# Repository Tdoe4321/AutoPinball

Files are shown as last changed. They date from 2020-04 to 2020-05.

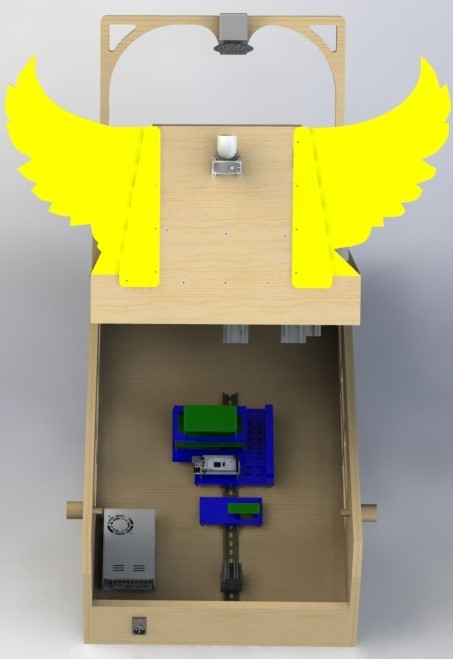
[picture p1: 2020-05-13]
CAD_Models/Play Field/Renderings/Final Renderings/Electronics 1.JPG

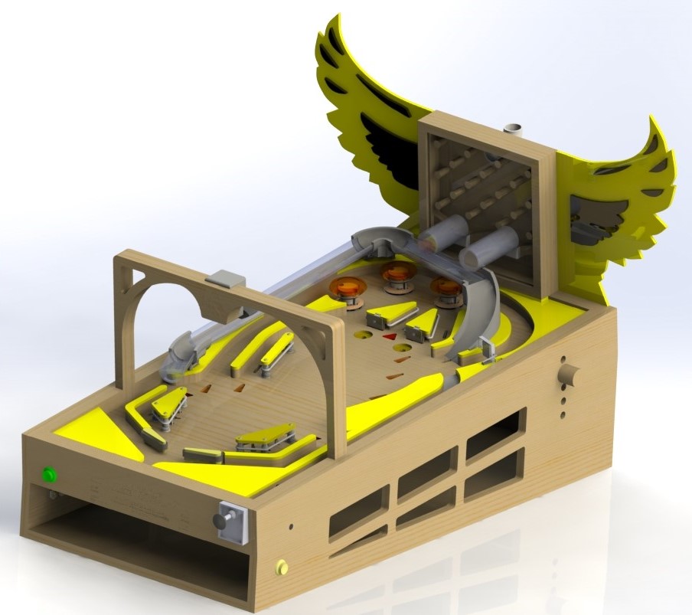
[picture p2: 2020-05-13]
CAD_Models/Play Field/Renderings/Isometric 4.JPG

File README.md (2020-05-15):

# AutoPinball
A custom pinball machine that plays itself!

[Checkout the full Instructables post!](https://www.instructables.com/id/Arduino-Pinball-Machine-That-Plays-Itself)

Check out the video here:  
AutoPinball Video (https://www.youtube.com/watch?v=dy7oVSNtaRk "AutoPinball")

Straight up demonstration of the autonomy here:  
AutoPinball Demonstration (https://www.youtube.com/watch?v=hW7z0yfWGfI "AutoPinball")

### Dependencies
This repo has the following dependencies that must be installed.
 * [ROS](http://wiki.ros.org/melodic/Installation/Ubuntu)
 * [rosserial_arduino](http://wiki.ros.org/rosserial_arduino/Tutorials/Arduino%20IDE%20Setup)
 * [OpenCV C++](https://opencv.org/)
 * [Tkinter](https://docs.python.org/3/library/tkinter.html)
 * [APScheduler](https://apscheduler.readthedocs.io/en/stable/)
 
To install ROS and rosserial_arduino, follow the links above and install as normal, for everything else, do the following:

```bash
sudo apt install libopencv-dev python3-opencv # OpenCV
sudo apt install python-tk # Tkinter
pip install APScheduler  # APScheduler
```
 
### Build
To build the system do the following:
```bash
cd /path/to/AutoPinball
mkdir build
cd build
cmake ..
make
source devel/setup.bash
```

After you build it, you can put the `source` command into your `~/.bashrc` to have it automatically source the directory whenever you start up a new bash shell. Just make sure that you give the full path, ex:  
`/home/<my-username>/AutoPinball/build/devel/setup.bash`

### RUN IT!
There's a few different launch files that you can use depending on what you want to do.
If you want to run the whole thing, run this one from the `launch` directory:  
```bash
roslaunch automatic_pinball_c.launch
```

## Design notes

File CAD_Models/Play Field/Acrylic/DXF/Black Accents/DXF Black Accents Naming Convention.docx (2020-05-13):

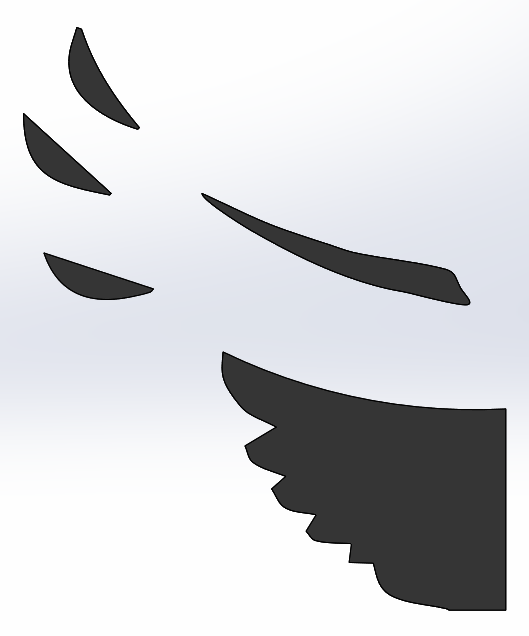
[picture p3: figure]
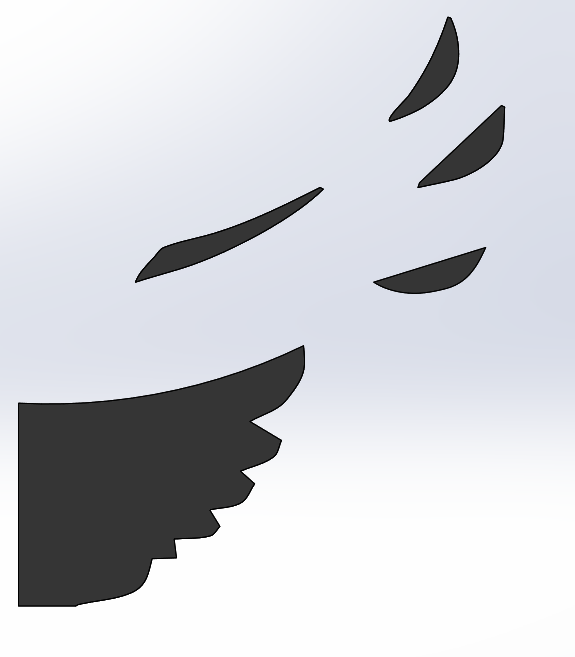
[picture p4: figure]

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
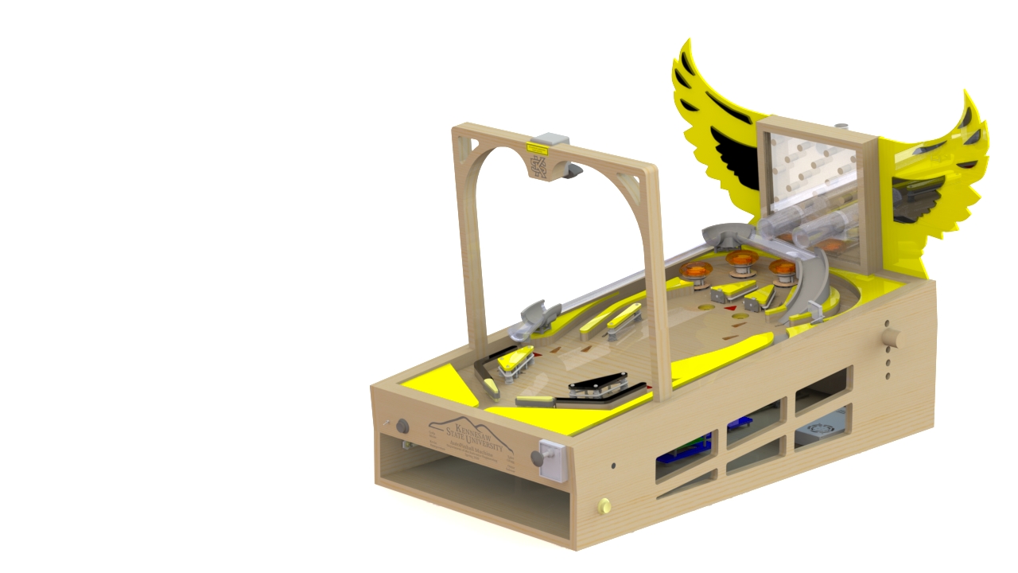
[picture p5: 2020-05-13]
CAD_Models/Play Field/Renderings/Final Renderings/16-9 Dimetric Thumbnail.JPG

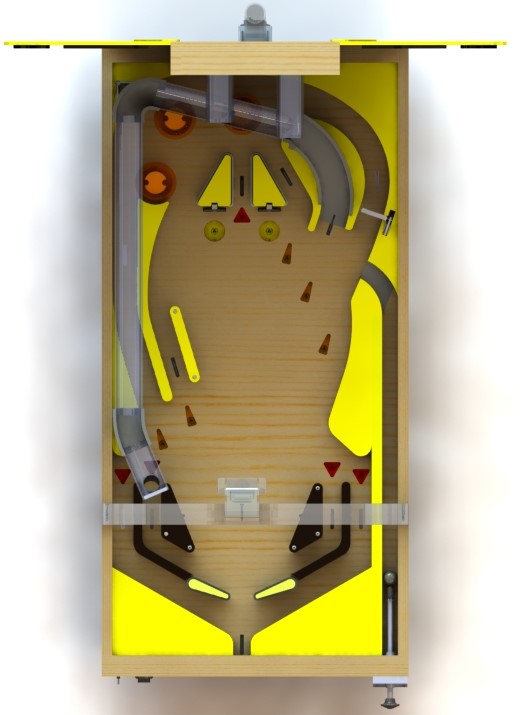
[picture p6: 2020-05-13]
CAD_Models/Play Field/Renderings/Final Renderings/Top 3.JPG

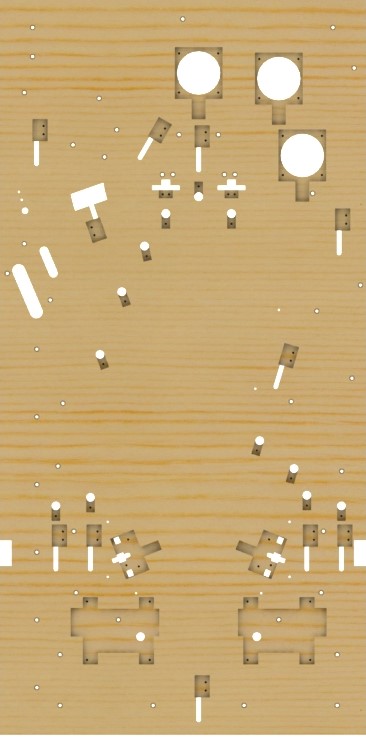
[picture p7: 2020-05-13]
CAD_Models/Play Field/Renderings/Final Renderings/Playfield Bottom 1.JPG

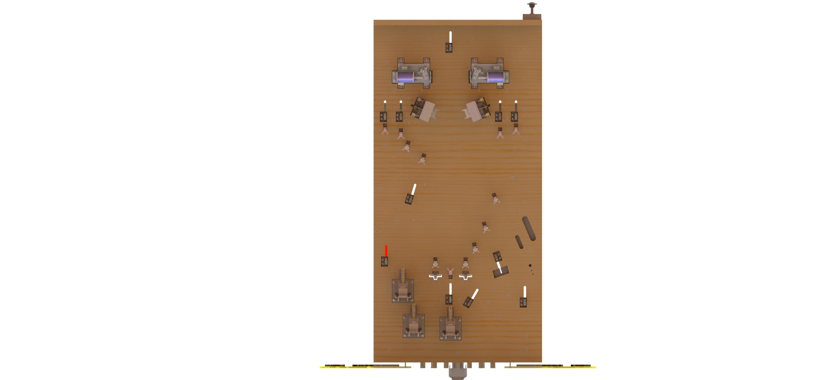
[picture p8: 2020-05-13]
CAD_Models/Play Field/Renderings/Bottom - 2.JPG

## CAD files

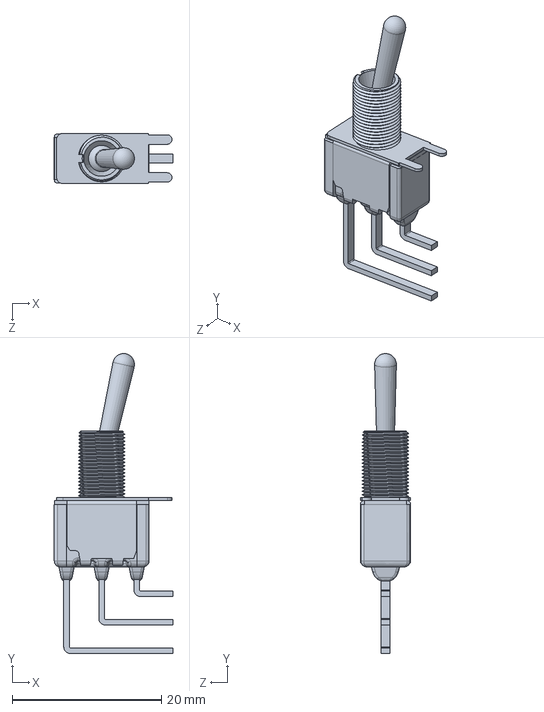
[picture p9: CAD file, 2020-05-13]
CAD_Models/Components/Electrical/7103SYAV2BE.SLDASM
15.9 x 40.2 x 6.76 mm

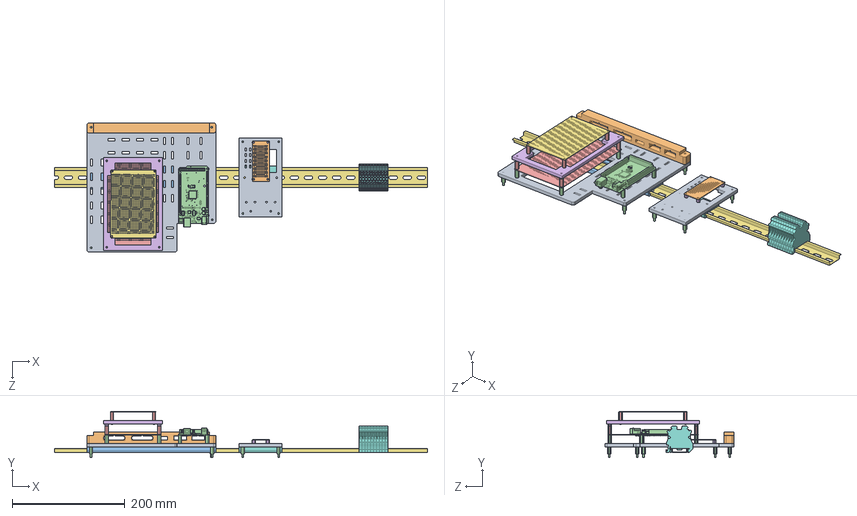
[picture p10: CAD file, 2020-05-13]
CAD_Models/Components/Electrical/Final_Pinball_Control_board/Main_Assembly/Final_Assembly.SLDASM
660.4 x 81.7 x 228.6 mm
Main board
Connector_Holder
Main board din_rail
arduinoMega
Flipper board
LED_mount
LED_control_board
Output board din rail
Output board
Output_Board
Spacer_Nut x 12
Spacer_.592 x 16
Spacer_.778 x 8
Spacer_..237 x 8
1.00m DIN Rail
UT_2.5_BK-select.stp x 10

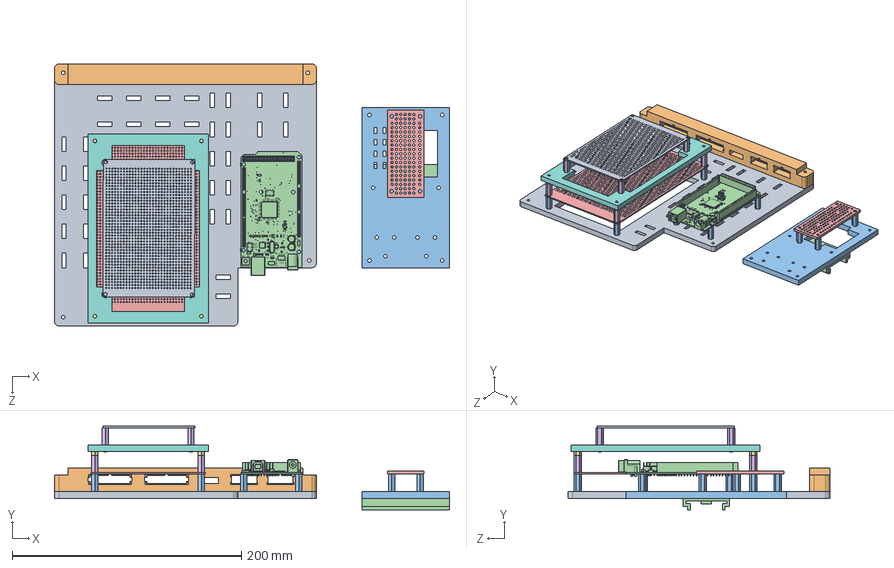
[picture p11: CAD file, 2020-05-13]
CAD_Models/Components/Electrical/Final_Pinball_Control_board_2/Main_Assembly/Final_Assembly.SLDASM
344.8 x 73.2 x 228.6 mm
Main board
Spacer_Nut x 18
Spacer_.592 x 12
arduinoMega
Flipper board
Spacer_.778 x 8
Spacer_..237 x 4
LED_mount
LED_control_board
Connector_Holder
Output board
Output

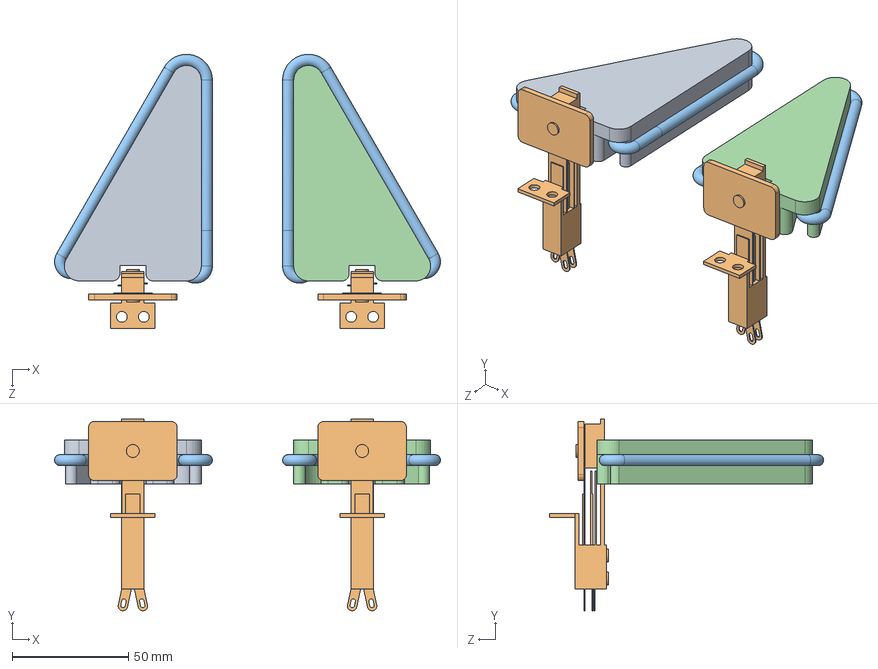
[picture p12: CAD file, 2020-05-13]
CAD_Models/Play Field/Play Items/Triangle Centerpiece Assembly R0.2.SLDASM
165.9 x 82.4 x 117.9 mm
Center Triangle Boundary R0.3
Stand-Up Target x 2
2.50 Elastic Band - Triangle x 2
Center Triangle Boundary R0.3 - Right

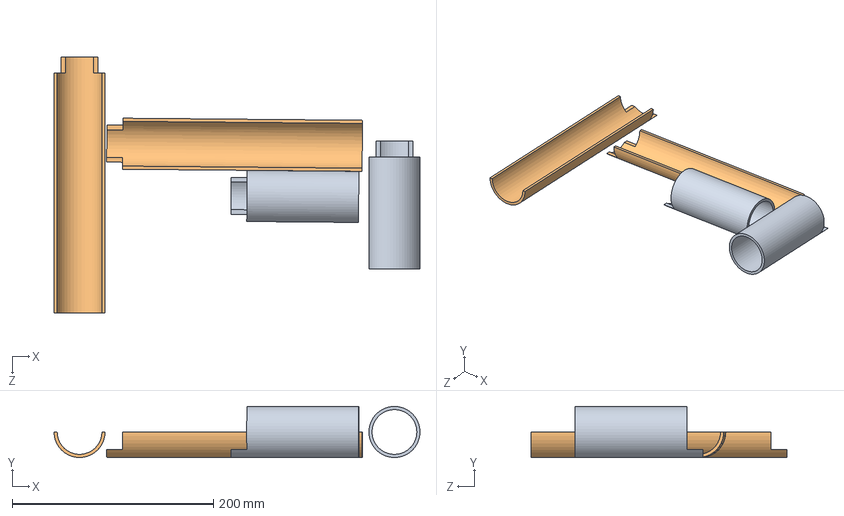
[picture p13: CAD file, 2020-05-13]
CAD_Models/Play Field/Reference & Testing/Tube Fitting Testing Assembly.SLDASM
363.8 x 50.8 x 254.0 mm
Pachinko Tube Acrylic x 2
Pachinko Tube Acrylic Halved x 2

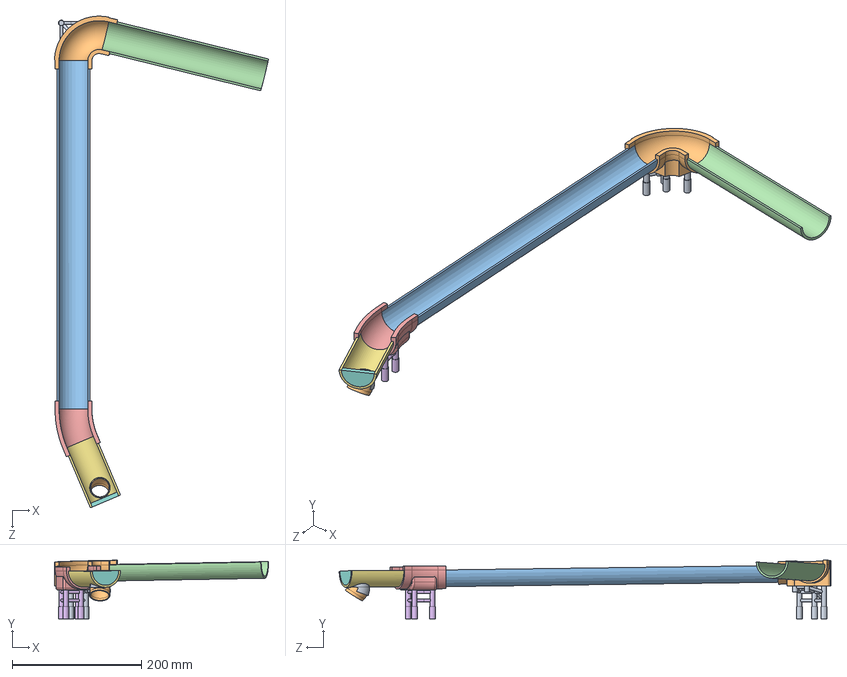
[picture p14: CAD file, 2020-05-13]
CAD_Models/Play Field/Second Level/Second Level Tube Assembly.SLDASM
331.5 x 90.9 x 761.6 mm
Joint 1 Mount
2.00 Acrylic Tube Adapter - 76.2deg
Level 2 Halved Tube - 2
Level 2 Halved Tube - 1
2.00 Acrylic Tube Adapter - 23.0deg
Joint 2 Mount R0.2
Level 2 Halved Tube - 3
1.75 x 0.125 Acrylic Tube End Cap - Halved
Second Level Drop Guide
Second Level Drop Guide R0.2

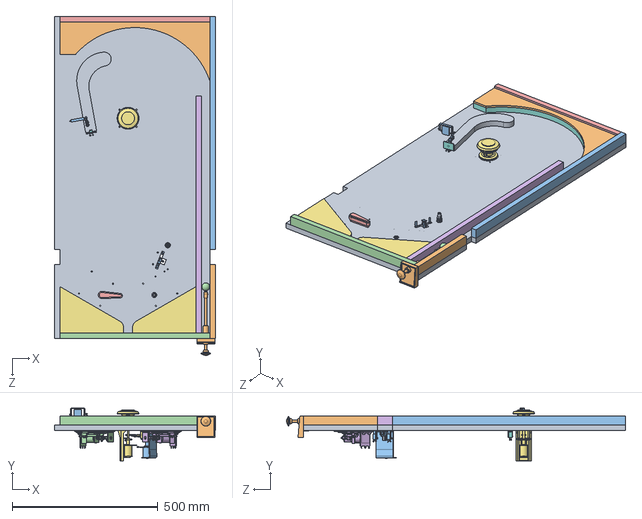
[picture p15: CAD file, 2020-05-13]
CAD_Models/Play Field/Subsystem Demo/AutoPinball Subsystem Demo Playfield.SLDASM
552.5 x 180.6 x 1163.4 mm

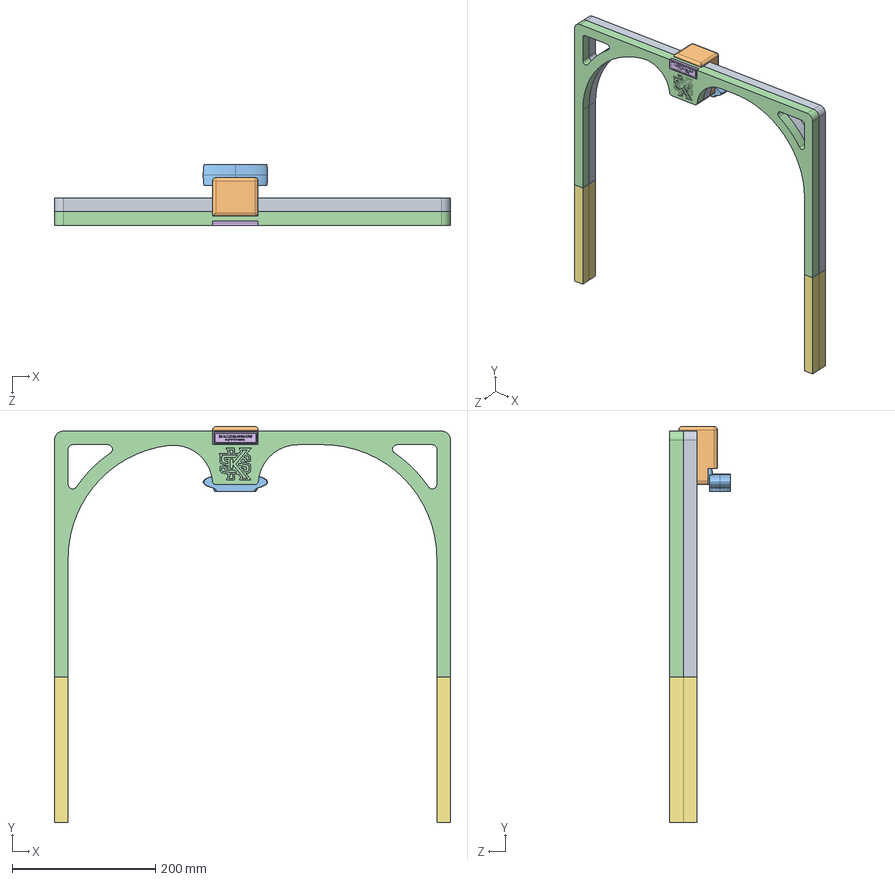
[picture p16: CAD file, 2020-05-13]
CAD_Models/Play Field/Camera Mount/Layered Concepts/Camera Mount Layered Concept 1.SLDASM
552.5 x 552.5 x 84.6 mm
Camera Mount Layered Concept 1
Camera Mount
Web Camera
Camera Mount Layered Concept 1 - Mirrored R0.2
#8 x 1.250 Flat Phillips Head for Wood AISI 304 x 3
Camera Mount Engraving Acrylic x 2
Camera Mount Leg Extensions x 4

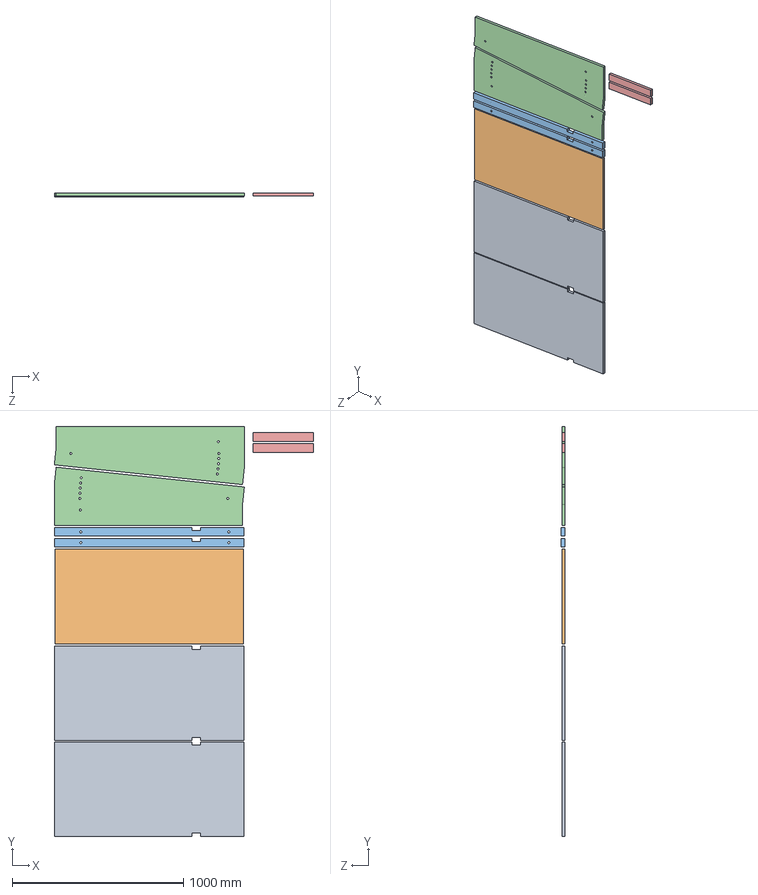
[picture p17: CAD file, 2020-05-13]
CAD_Models/Play Field/Reference & Testing/Plywood Order.SLDASM
1513.9 x 2392.7 x 25.4 mm
Base Layer R0.2 x 2
Base Stand
Playfield Support Strut x 2
Side Stand R0.2 x 2
Camera Mount Support Strut x 2

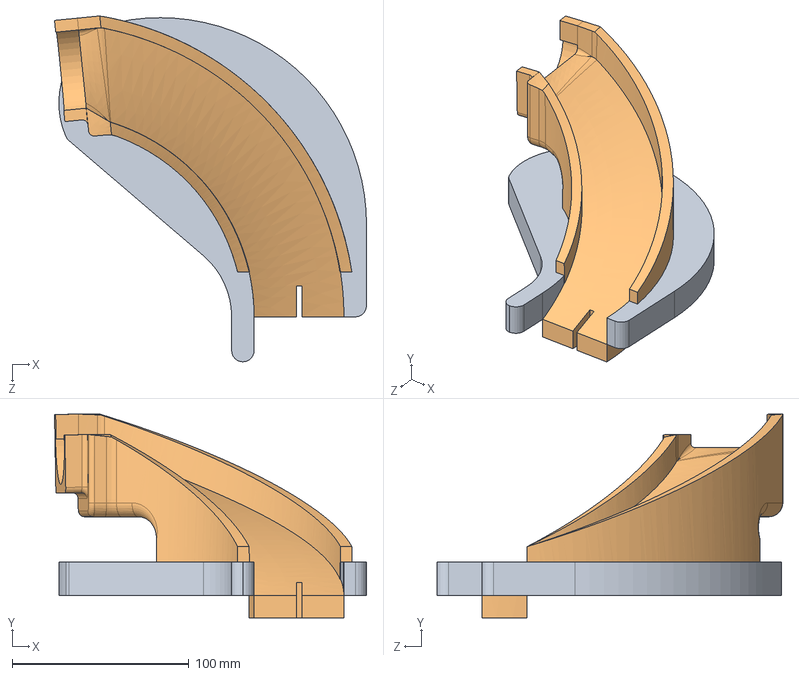
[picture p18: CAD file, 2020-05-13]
CAD_Models/Play Field/Second Level/Playfield Ramp Assembly.SLDASM
176.4 x 115.2 x 195.4 mm
Ramp Base Mount
Playfield Ramp
#8-32 x 0.321 Brass Flanged Heat Insert x 4

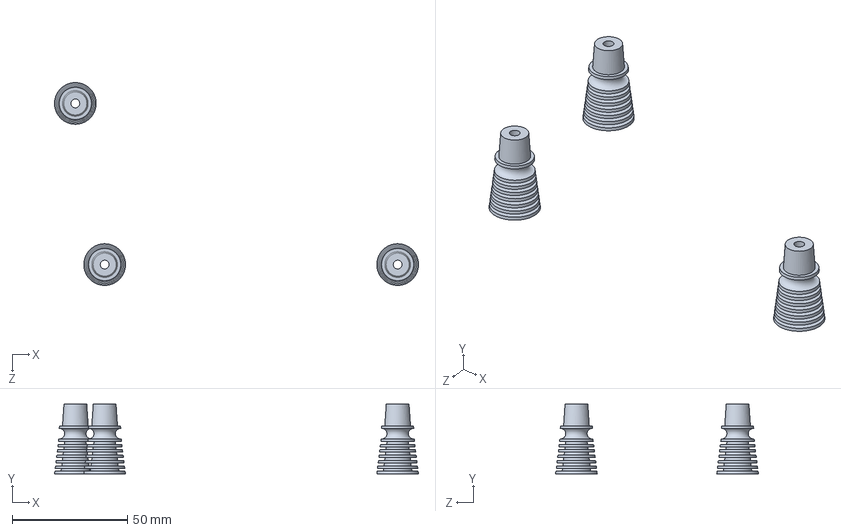
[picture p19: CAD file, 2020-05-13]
CAD_Models/Components/3.00 Elastic Band Triangle.SLDASM
157.8 x 30.2 x 87.9 mm
Star Post - Clear x 3

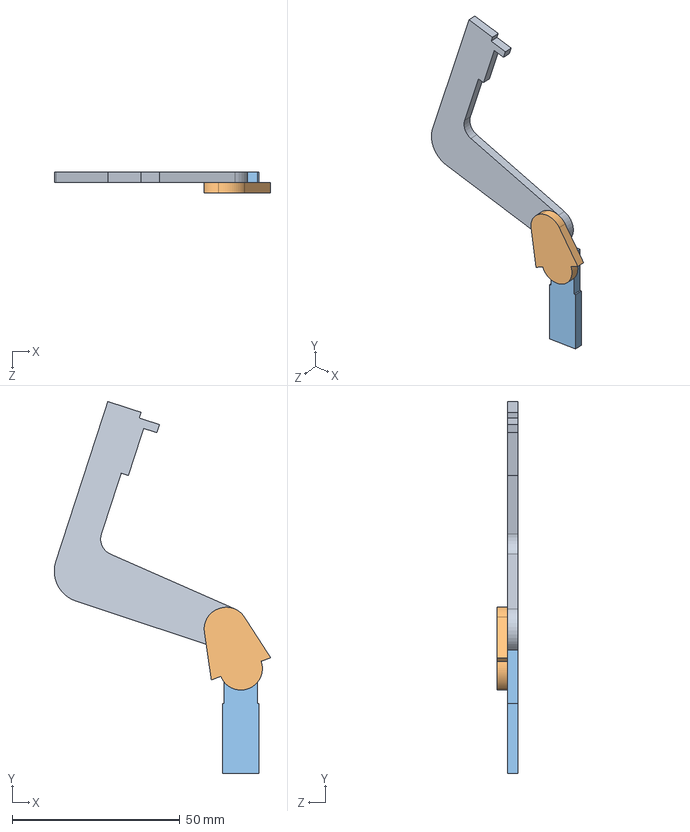
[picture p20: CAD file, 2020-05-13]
CAD_Models/Components/Cams/Slingshot Test Cam Assembly.SLDASM
64.4 x 110.7 x 6.35 mm
Slingshot Test Cam
Slingshot Test Cam Adapter
Slingshot Test Cam Solenoid Rod

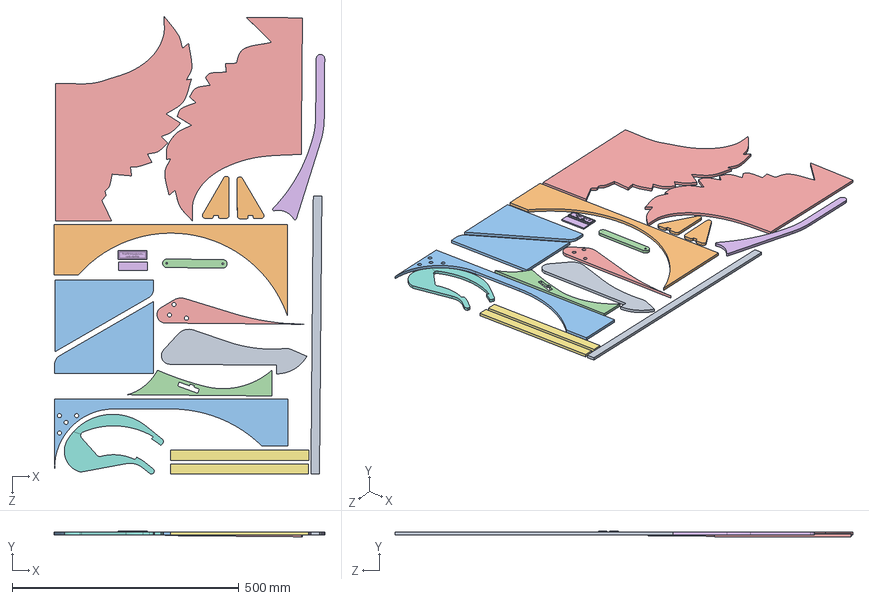
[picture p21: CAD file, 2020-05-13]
CAD_Models/Play Field/Acrylic/Yellow Acrylic Layout.SLDASM
596.0 x 12.4 x 1008.9 mm
Shooter Trim Acrylic
Center Triangle Boundary R0.3 Acrylic x 2
Front Apron Acrylic x 2
Launch Lane Exit Guard - Right Acrylic
Left Outlane Guard Acrylic
Left Y-Lane Trim Acrylic
Pachinko Machine Shim Acrylic x 2
Ramp Base Mount Acrylic
Right Outlane Guard Acrylic
Top Apron Acrylic
Top Apron Acrylic R0.2
Y-Lane Elastic Acrylic
KSU Owl Wings - Left x 2
Camera Mount Engraving Acrylic x 2

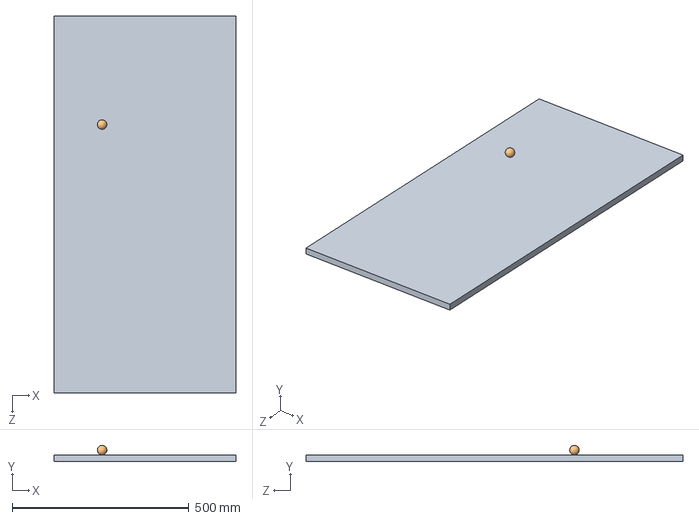
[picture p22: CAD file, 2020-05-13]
CAD_Models/Play Field/AutoPinball Playfield R0.1.SLDASM
514.3 x 46.0 x 1066.8 mm
Base Layer 6deg Gradient
Standard Pinball

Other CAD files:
CAD_Models/Play Field/CNC/Extra/THRU MILL AND 0.25 DP MILL AND 0.125 X 0.4375 DP BIT AND 0.125 THRU ALL BIT - EXTRA.SLDASM
CAD_Models/Play Field/CNC/THRU MILL 2D LAYOUT - EXTRA/THRU MILL 2D LAYOUT - EXTRA.SLDASM
CAD_Models/Play Field/CNC/THRU MILL AND 0.125 X 0.4375 DP BIT - EXTRA/THRU MILL AND 0.125 X 0.4375 DP BIT - EXTRA.SLDASM
CAD_Models/Play Field/CNC/Stand/THRU MILL - STAND.SLDASM
CAD_Models/Components/0.25 x 20 x 1.25 Five Arm Knob.SLDPRT
CAD_Models/Components/2.0 Elastic Band - Y-Lane.SLDPRT
CAD_Models/Components/2.00 Elastic Band - Slingshot.SLDPRT
CAD_Models/Components/2.00 Elastic Band Triangle R0.2.SLDASM
CAD_Models/Components/2.00 Elastic Band Triangle.SLDASM
CAD_Models/Components/2.25 Elastic Band - Y-Lane.SLDPRT
CAD_Models/Components/2.25 Elastic Band Triangle R0.2.SLDASM
CAD_Models/Components/2.25 Elastic Band Triangle.SLDASM
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

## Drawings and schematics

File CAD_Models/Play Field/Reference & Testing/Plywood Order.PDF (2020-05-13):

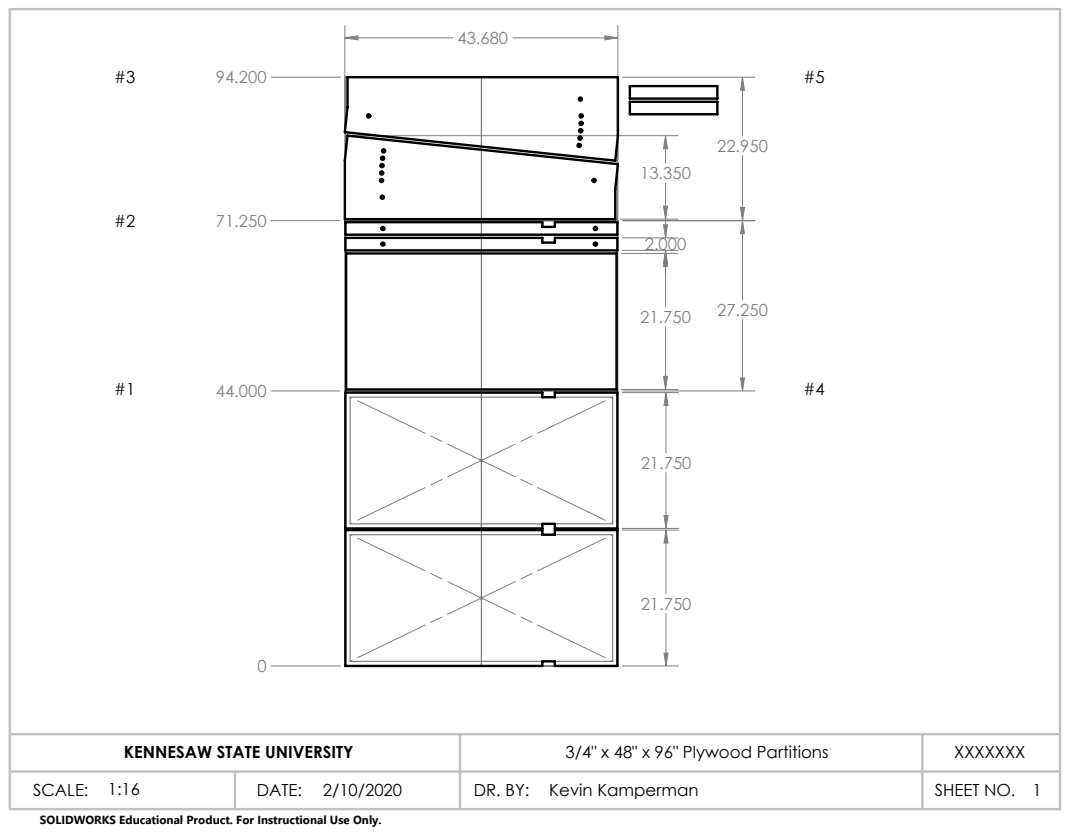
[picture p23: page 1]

KENNESAW STATE UNIVERSITY | 3/4" x 48" x 96" Plywood Partitions | XXXXXXX

1:16 SCALE: | DATE: 2/10/2020 | DR. BY: Kevin Kamperman | SHEET NO. 1

SOLIDWORKS Educational Product. For Instructional Use Only.

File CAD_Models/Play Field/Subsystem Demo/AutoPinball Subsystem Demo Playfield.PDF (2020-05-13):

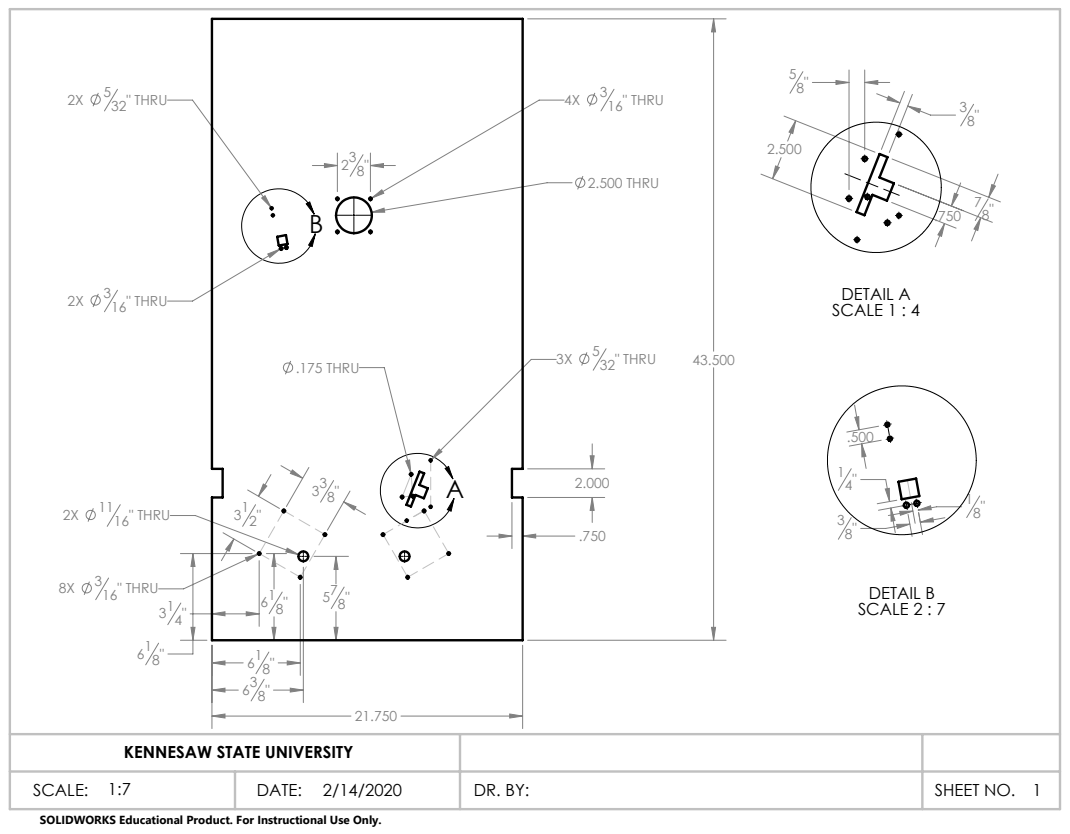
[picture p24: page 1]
2.500 THRU; " THRU 5; 32" THRU; 2X 3 16" THRU; .175 THRU; 8X 3 16" THRU; 2X 11 16" THRU; DETAIL A SCALE 1 : 4; DETAIL B SCALE 2 : 7

KENNESAW STATE UNIVERSITY

SCALE: 1:7 | DATE: 2/14/2020 | DR. BY: | SHEET NO. 1

SOLIDWORKS Educational Product. For Instructional Use Only.

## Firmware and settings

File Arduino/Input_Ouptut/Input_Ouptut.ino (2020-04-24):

/*
 * Author: Tyler Gragg
 * Date First Created: 01/18/2020
 * Project: AutoPinball
 */

#include <ros.h>
#include <std_msgs/Int32.h>
#include <std_msgs/UInt16.h>
#include <std_msgs/Bool.h>
#include <Servo.h>

// Flipper Outputs
#define LeftFlipper 20
#define RightFlipper 21


// Switch Inputs - Playfield
// TOP
#define TopSwitch0 8  // Rollover
#define TopSwitch1 49 // Bumper
#define TopSwitch2 50 // Bumper
#define TopSwitch3 51 // Bumper
#define TopSwitch4 5  // Rollover
#define TopSwitch5 15 // Spinner

// MID
#define MidSwitch0 9  // Rollover
#define MidSwitch1 13 // Standup
#define MidSwitch2 7  // Rollover
#define MidSwitch3 14 // Standup
#define MidSwitch4 6  // Rollover
#define MidSwitch5 4  // Rollover

//BOT
#define BotSwitch0 10 // Rollover
#define BotSwitch1 11 // Rollover
#define BotSwitch2 53 // Slingshot
#define BotSwitch3 52 // Slingshot
#define BotSwitch4 3  // Rollover
#define BotSwitch5 2  // Rollover
#define BotSwitch6 18 // Flipper
#define BotSwitch7 19 // Flipper
#define BotSwitch8 12 // Rollover

// Light Outputs
// TOP
#define TopLight0 36
#define TopLight1 35
#define TopLight2 34

// MID
#define MidLight0 31
#define MidLight1 32
#define MidLight2 27
#define MidLight3 28
#define MidLight4 29
#define MidLight5 26
#define MidLight6 25
#define MidLight7 24

// BOT
#define BotLight0 33
#define BotLight1 30
#define BotLight2 23
#define BotLight3 22

// Coils
#define Coil0 44
#define Coil1 45
#define Coil2 46
#define Coil3 47
#define Coil4 48

// Start button & Autonomy Switch
#define StartButton 42
#define AutonomySwitch 43

// Servo for the multiball
#define ServoPin A0
Servo multiball; 

// Last states
// TOP
uint8_t TopSwitch0Last = 0;
uint8_t TopSwitch1Last = 0;
uint8_t TopSwitch2Last = 0;
uint8_t TopSwitch3Last = 0;
uint8_t TopSwitch4Last = 0;
uint8_t TopSwitch5Last = 0;

// MID
uint8_t MidSwitch0Last = 0;
uint8_t MidSwitch1Last = 0;
uint8_t MidSwitch2Last = 0;
uint8_t MidSwitch3Last = 0;
uint8_t MidSwitch4Last = 0;
uint8_t MidSwitch5Last = 0;

// BOT
uint8_t BotSwitch0Last = 0;
uint8_t BotSwitch1Last = 0;
uint8_t BotSwitch2Last = 0;
uint8_t BotSwitch3Last = 0;
uint8_t BotSwitch4Last = 0;
uint8_t BotSwitch5Last = 0;
uint8_t BotSwitch6Last = 0;
uint8_t BotSwitch7Last = 0;
uint8_t BotSwitch8Last = 0;

uint8_t StartButtonLast = 0;
uint8_t AutonomySwitchLast = 0;

// ROS Node Handle
ros::NodeHandle nh;

// ROS Published messages
std_msgs::Bool empty_msg;

// TOP
ros::Publisher switch_top_0_pub("switch_top_0_triggered", &empty_msg);
ros::Publisher switch_top_1_pub("switch_top_1_triggered", &empty_msg);
ros::Publisher switch_top_2_pub("switch_top_2_triggered", &empty_msg);
ros::Publisher switch_top_3_pub("switch_top_3_triggered", &empty_msg);
ros::Publisher switch_top_4_pub("switch_top_4_triggered", &empty_msg);
ros::Publisher switch_top_5_pub("switch_top_5_triggered", &empty_msg);

// MID
ros::Publisher switch_mid_0_pub("switch_mid_0_triggered", &empty_msg);
ros::Publisher switch_mid_1_pub("switch_mid_1_triggered", &empty_msg);
ros::Publisher switch_mid_2_pub("switch_mid_2_triggered", &empty_msg);
ros::Publisher switch_mid_3_pub("switch_mid_3_triggered", &empty_msg);
ros::Publisher switch_mid_4_pub("switch_mid_4_triggered", &empty_msg);
ros::Publisher switch_mid_5_pub("switch_mid_5_triggered", &empty_msg);

// BOT
ros::Publisher switch_bot_0_pub("switch_bot_0_triggered", &empty_msg);
ros::Publisher switch_bot_1_pub("switch_bot_1_triggered", &empty_msg);
ros::Publisher switch_bot_2_pub("switch_bot_2_triggered", &empty_msg);
ros::Publisher switch_bot_3_pub("switch_bot_3_triggered", &empty_msg);
ros::Publisher switch_bot_4_pub("switch_bot_4_triggered", &empty_msg);
ros::Publisher switch_bot_5_pub("switch_bot_5_triggered", &empty_msg);
ros::Publisher switch_bot_6_pub("switch_bot_6_triggered", &empty_msg);
ros::Publisher switch_bot_7_pub("switch_bot_7_triggered", &empty_msg);
ros::Publisher switch_bot_8_pub("switch_bot_8_triggered", &empty_msg);

ros::Publisher start_button_pub("switch_start_button_triggered", &empty_msg);
ros::Publisher autonomy_switch_pub("switch_autonomy_switch_triggered", &empty_msg);

void flip_callback(const std_msgs::Int32& flipper){
  // 1 = left_flipper ON, 2 = right_flipper ON, -1 = left_flipper OFF, -2 = right_flipper OFF
  if (flipper.data == 1){
    digitalWrite(LeftFlipper, HIGH);
  }
  else if(flipper.data == 2){
    digitalWrite(RightFlipper, HIGH); 
  }
  else if(flipper.data == -1){
    digitalWrite(LeftFlipper, LOW);
  }
  else if(flipper.data == -2){
    digitalWrite(RightFlipper, LOW);
  }
}

// Turn on whatever int comes in
void pin_on_callback(const std_msgs::Int32& pin){
  digitalWrite(pin.data, HIGH);
}

// Turn off whatever int comes in
void pin_off_callback(const std_msgs::Int32& pin){
  digitalWrite(pin.data, LOW);
}

// Write the servo to whatever comes in
void servo_value_callback(const std_msgs::UInt16& value){
  multiball.writeMicroseconds(value.data); 
}


// ROS Subscibed messages
ros::Subscriber<std_msgs::Int32> flip_sub("flip_flipper", &flip_callback);
ros::Subscriber<std_msgs::Int32> pin_on_sub("pin_on", &pin_on_callback);
ros::Subscriber<std_msgs::Int32> pin_off_sub("pin_off", &pin_off_callback);
ros::Subscriber<std_msgs::UInt16> multiball_servo_sub("servo_value", &servo_value_callback);

// Check all switches, then publish if they are triggered
void checkSwitches(){
  //TOP
  uint8_t curTopSwitch0 = digitalRead(TopSwitch0);
  uint8_t curTopSwitch1 = digitalRead(TopSwitch1);
  uint8_t curTopSwitch2 = digitalRead(TopSwitch2);
  uint8_t curTopSwitch3 = digitalRead(TopSwitch3);
  uint8_t curTopSwitch4 = digitalRead(TopSwitch4);
  uint8_t curTopSwitch5 = digitalRead(TopSwitch5);

  //MID
  uint8_t curMidSwitch0 = digitalRead(MidSwitch0);
  uint8_t curMidSwitch1 = digitalRead(MidSwitch1);
  uint8_t curMidSwitch2 = digitalRead(MidSwitch2);
  uint8_t curMidSwitch3 = digitalRead(MidSwitch3);
  uint8_t curMidSwitch4 = digitalRead(MidSwitch4);
  uint8_t curMidSwitch5 = digitalRead(MidSwitch5);
  
  //BOT
  uint8_t curBotSwitch0 = digitalRead(BotSwitch0);
  uint8_t curBotSwitch1 = digitalRead(BotSwitch1);
  uint8_t curBotSwitch2 = digitalRead(BotSwitch2);
  uint8_t curBotSwitch3 = digitalRead(BotSwitch3);
  uint8_t curBotSwitch4 = digitalRead(BotSwitch4);
  uint8_t curBotSwitch5 = digitalRead(BotSwitch5);
  uint8_t curBotSwitch6 = digitalRead(BotSwitch6);
  uint8_t curBotSwitch7 = digitalRead(BotSwitch7);
  uint8_t curBotSwitch8 = digitalRead(BotSwitch8);

  uint8_t curStartButton = digitalRead(StartButton);
  uint8_t curAutonomySwitch = digitalRead(AutonomySwitch);
  
  // -----------  TOP  -----------
  if (!curTopSwitch0 && curTopSwitch0 != TopSwitch0Last){
    switch_top_0_pub.publish(&empty_msg);
    nh.spinOnce();
  }
  if (!curTopSwitch1 && curTopSwitch1 != TopSwitch1Last){
    switch_top_1_pub.publish(&empty_msg);
    nh.spinOnce();
  }
  if (!curTopSwitch2 && curTopSwitch2 != TopSwitch2Last){
    switch_top_2_pub.publish(&empty_msg);
    nh.spinOnce();
  }
  if (!curTopSwitch3 && curTopSwitch3 != TopSwitch3Last){
    switch_top_3_pub.publish(&empty_msg);
    nh.spinOnce();
  }
  if (!curTopSwitch4 && curTopSwitch4 != TopSwitch4Last){
    switch_top_4_pub.publish(&empty_msg);
    nh.spinOnce();
  }
  if (!curTopSwitch5 && curTopSwitch5 != TopSwitch5Last){
    switch_top_5_pub.publish(&empty_msg);
    nh.spinOnce();
  }

  // -----------  MID  -----------
  if (!curMidSwitch0 && curMidSwitch0 != MidSwitch0Last){
    switch_mid_0_pub.publish(&empty_msg);
    nh.spinOnce();
  }
  if (!curMidSwitch1 && curMidSwitch1 != MidSwitch1Last){
    switch_mid_1_pub.publish(&empty_msg);
    nh.spinOnce();
  }
  if (!curMidSwitch2 && curMidSwitch2 != MidSwitch2Last){
    switch_mid_2_pub.publish(&empty_msg);
    nh.spinOnce();
  }
  if (!curMidSwitch3 && curMidSwitch3 != MidSwitch3Last){
    switch_mid_3_pub.publish(&empty_msg);
    nh.spinOnce();
  }
  if (!curMidSwitch4 && curMidSwitch4 != MidSwitch4Last){
    switch_mid_4_pub.publish(&empty_msg);
    nh.spinOnce();
  }
  if (!curMidSwitch5 && curMidSwitch5 != MidSwitch5Last){
    switch_mid_5_pub.publish(&empty_msg);
    nh.spinOnce();
  }

  // -----------  BOT  -----------
  if (!curBotSwitch0 && curBotSwitch0 != BotSwitch0Last){
    switch_bot_0_pub.publish(&empty_msg);
    nh.spinOnce();
  }
  if (!curBotSwitch1 && curBotSwitch1 != BotSwitch1Last){
    switch_bot_1_pub.publish(&empty_msg);
    nh.spinOnce();
  }
  if (!curBotSwitch2 && curBotSwitch2 != BotSwitch2Last){
    switch_bot_2_pub.publish(&empty_msg);
    nh.spinOnce();
  }
  if (!curBotSwitch3 && curBotSwitch3 != BotSwitch3Last){
    switch_bot_3_pub.publish(&empty_msg);
    nh.spinOnce();
  }
  if (!curBotSwitch4 && curBotSwitch4 != BotSwitch4Last){
    switch_bot_4_pub.publish(&empty_msg);
    nh.spinOnce();
  }
  if (!curBotSwitch5 && curBotSwitch5 != BotSwitch5Last){
    switch_bot_5_pub.publish(&empty_msg);
    nh.spinOnce();
  }
  if (curBotSwitch6 && curBotSwitch6 != BotSwitch6Last){ // FLIPPER - different logic
    switch_bot_6_pub.publish(&empty_msg);
    nh.spinOnce();
  }
  if (curBotSwitch7 && curBotSwitch7 != BotSwitch7Last){ // FLIPPER - different logic
    switch_bot_7_pub.publish(&empty_msg);
    nh.spinOnce();
  }
  if (!curBotSwitch8 && curBotSwitch8 != BotSwitch8Last){
    switch_bot_8_pub.publish(&empty_msg);
    nh.spinOnce();
  }

  // -----------  OTHER  -----------
  if (!curStartButton && curStartButton != StartButtonLast){
    start_button_pub.publish(&empty_msg);
    nh.spinOnce();
  }
  if (curAutonomySwitch!= AutonomySwitchLast){
    empty_msg.data = !curAutonomySwitch;
    autonomy_switch_pub.publish(&empty_msg);
    nh.spinOnce();
  }

  //TOP
  TopSwitch0Last = curTopSwitch0;
  TopSwitch1Last = curTopSwitch1;
  TopSwitch2Last = curTopSwitch2;
  TopSwitch3Last = curTopSwitch3;
  TopSwitch4Last = curTopSwitch4;
  TopSwitch5Last = curTopSwitch5;
    
  //MID
  MidSwitch0Last = curMidSwitch0;
  MidSwitch1Last = curMidSwitch1;
  MidSwitch2Last = curMidSwitch2;
  MidSwitch3Last = curMidSwitch3;
  MidSwitch4Last = curMidSwitch4;
  MidSwitch5Last = curMidSwitch5;
  
  //BOT
  BotSwitch0Last = curBotSwitch0;
  BotSwitch1Last = curBotSwitch1;
  BotSwitch2Last = curBotSwitch2;
  BotSwitch3Last = curBotSwitch3;
  BotSwitch4Last = curBotSwitch4;
  BotSwitch5Last = curBotSwitch5;
  BotSwitch6Last = curBotSwitch6;
  BotSwitch7Last = curBotSwitch7;
  BotSwitch8Last = curBotSwitch8;

  //OTHER
  StartButtonLast = curStartButton;
  AutonomySwitchLast = curAutonomySwitch;
}

void setup(){
  //Flippers
  pinMode(LeftFlipper, OUTPUT);
  pinMode(RightFlipper, OUTPUT);
  
  // Start Button & Autonomy
  pinMode(StartButton, INPUT_PULLUP);
  pinMode(AutonomySwitch, INPUT_PULLUP);
  
  // Switches
  //TOP
  pinMode(TopSwitch0, INPUT_PULLUP);
  pinMode(TopSwitch1, INPUT_PULLUP);
  pinMode(TopSwitch2, INPUT_PULLUP);
  pinMode(TopSwitch3, INPUT_PULLUP);
  pinMode(TopSwitch4, INPUT_PULLUP);
  pinMode(TopSwitch5, INPUT_PULLUP);
  
  //MID
  pinMode(MidSwitch0, INPUT_PULLUP);
  pinMode(MidSwitch1, INPUT_PULLUP);
  pinMode(MidSwitch2, INPUT_PULLUP);
  pinMode(MidSwitch3, INPUT_PULLUP);
  pinMode(MidSwitch4, INPUT_PULLUP);
  pinMode(MidSwitch5, INPUT_PULLUP);
  
  //BOT
  pinMode(BotSwitch0, INPUT_PULLUP);
  pinMode(BotSwitch1, INPUT_PULLUP);
  pinMode(BotSwitch2, INPUT_PULLUP);
  pinMode(BotSwitch3, INPUT_PULLUP);
  pinMode(BotSwitch4, INPUT_PULLUP);
  pinMode(BotSwitch5, INPUT_PULLUP);
  pinMode(BotSwitch6, INPUT); // FLIPPER - different logic
  pinMode(BotSwitch7, INPUT); // FLIPPER - different logic
  pinMode(BotSwitch8, INPUT_PULLUP);
  
  // Lights
  //TOP
  pinMode(TopLight0, OUTPUT);
  pinMode(TopLight1, OUTPUT);
  pinMode(TopLight2, OUTPUT);
  
  //MID
  pinMode(MidLight0, OUTPUT);
  pinMode(MidLight1, OUTPUT);
  pinMode(MidLight2, OUTPUT);
  pinMode(MidLight3, OUTPUT);
  pinMode(MidLight4, OUTPUT);
  pinMode(MidLight5, OUTPUT);
  pinMode(MidLight6, OUTPUT);
  pinMode(MidLight7, OUTPUT);
  
  //BOT
  pinMode(BotLight0, OUTPUT);
  pinMode(BotLight1, OUTPUT);
  pinMode(BotLight2, OUTPUT);
  pinMode(BotLight3, OUTPUT);

  //Coils
  pinMode(Coil0, OUTPUT);
  pinMode(Coil1, OUTPUT);
  pinMode(Coil2, OUTPUT);
  pinMode(Coil3, OUTPUT);
  pinMode(Coil4, OUTPUT);

  // Servo
  multiball.attach(ServoPin);

  // Set everything low to start out
  digitalWrite(LeftFlipper, LOW);
  digitalWrite(RightFlipper, LOW);
  digitalWrite(TopLight0, LOW);
  digitalWrite(TopLight1, LOW);
  digitalWrite(TopLight2, LOW);
  digitalWrite(MidLight0, LOW);
  digitalWrite(MidLight1, LOW);
  digitalWrite(MidLight2, LOW);
  digitalWrite(MidLight3, LOW);
  digitalWrite(MidLight4, LOW);
  digitalWrite(MidLight5, LOW);
  digitalWrite(MidLight6, LOW);
  digitalWrite(MidLight7, LOW);
  digitalWrite(BotLight0, LOW);
  digitalWrite(BotLight1, LOW);
  digitalWrite(BotLight2, LOW);
  digitalWrite(BotLight3, LOW);
  digitalWrite(Coil0, LOW);
  digitalWrite(Coil1, LOW);
  digitalWrite(Coil2, LOW);
  digitalWrite(Coil3, LOW);
  digitalWrite(Coil4, LOW);
  multiball.writeMicroseconds(2000);
  
  // Initialize ROS stuff
  nh.initNode();
  
  //TOP
  nh.advertise(switch_top_0_pub);
  nh.advertise(switch_top_1_pub);
  nh.advertise(switch_top_2_pub);
  nh.advertise(switch_top_3_pub);
  nh.advertise(switch_top_4_pub);
  nh.advertise(switch_top_5_pub);

  //MID
  nh.advertise(switch_mid_0_pub);
  nh.advertise(switch_mid_1_pub);
  nh.advertise(switch_mid_2_pub);
  nh.advertise(switch_mid_3_pub);
  nh.advertise(switch_mid_4_pub);
  nh.advertise(switch_mid_5_pub);
  
  //BOT
  nh.advertise(switch_bot_0_pub);
  nh.advertise(switch_bot_1_pub);
  nh.advertise(switch_bot_2_pub);
  nh.advertise(switch_bot_3_pub);
  nh.advertise(switch_bot_4_pub);
  nh.advertise(switch_bot_5_pub);
  nh.advertise(switch_bot_6_pub);
  nh.advertise(switch_bot_7_pub);
  nh.advertise(switch_bot_8_pub);

  //OTHER
  nh.advertise(start_button_pub);
  nh.advertise(autonomy_switch_pub);
  
  // Subscribers
  nh.subscribe(flip_sub);
  nh.subscribe(pin_on_sub);
  nh.subscribe(pin_off_sub);
  nh.subscribe(multiball_servo_sub);

  // Boolean empty message
  empty_msg.data = true;
}

void loop(){
  checkSwitches();
  nh.spinOnce();
}

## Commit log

2020-01-18 Added a rough block up of the arduino code
2020-01-20 Integrated hardware, fixed minor bugs
    [Input_Ouptut.ino]
2020-01-21 Fixed callback for lights on and off
    [Input_Ouptut.ino]
2020-01-23 Added information that is relevant to lights and switches
2020-01-25 Added individual publisher for each switch on playfield
2020-01-31 Custom srv to get a reference to switches and lights on the playfield
2020-01-31 Updating list of what switches have been previously triggered
2020-01-31 Implemented Idle state and resetting via start button
2020-02-03 Added more IO for arduino
2020-02-14 Changed colors, scores, added idle catch case
2020-03-06 Send ROS message on flip, track flipping, so we don't detect flippers moved
2020-03-13 Pin numbers changed to reflect the real playfield
2020-03-13 PDR pin numbers and play
2020-03-13 Integration Demo Pin Numbers
2020-03-16 Testing the camera flipping on the real test-bed
2020-03-16 Update Switch_top_1 to include debounce
2020-03-21 Added ability to track flippers
2020-04-07 Added ability to change camera number easily
2020-04-17 pin numbers (mostly) all correct. Shift operator added. Lots of little things
    [Input_Ouptut.ino]
2020-04-17 Updated camera path
2020-04-18 Tune camera for Kevin's garage
2020-04-18 More camera tuning
2020-04-18 Added arduino start button numbers
2020-04-20 Added support for using the autonomy enabled switch
2020-04-20 Updated low_level to include autonomy mode easy switching. Also, some multiball stuff that doesn't work
    [Input_Ouptut.ino]
2020-05-13 CAD models uploaded
    [#10-32 x 0.500 Pan Phillips Head for Sheet Metal AISI 304.SLDPRT, #4 x 1.250 Flat Phillips Head Zinc Plated Steel.SLDPRT, #8 x 1.000 Flat Phillips Head for Woo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]
